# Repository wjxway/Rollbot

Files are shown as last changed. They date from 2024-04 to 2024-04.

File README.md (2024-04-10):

# Rollbot: a Spherical Robot Driven by a Single Actuator

Paper can be fetched from [Arxiv](https://arxiv.org/abs/2404.05120).

This repo is the full implementation of Rollbot, including complete hardware, software, theoretical derivation files.

It's still under construction, so the files might be a bit messy. I will clean it up once the paper is officially accepted.

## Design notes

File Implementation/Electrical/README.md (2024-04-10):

This is just a power converter from 4s battery down to 3.3V. Feel free to create your own.

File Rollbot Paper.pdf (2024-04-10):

## Rollbot: a Spherical Robot Driven by a Single Actuator

Jingxian Wang¹

and Michael Rubenstein¹

Abstract— Here we present Rollbot, the first spherical robot capable of controllably maneuvering on 2D plane with a single actuator. Rollbot rolls on the ground in circular pattern and controls its motion by changing the curvature of the trajectory through accelerating and decelerating its single motor and attached mass. We present the theoretical analysis, design, and control of Rollbot, and demonstrate its ability to move in a controllable circular pattern and follow waypoints.

I. INTRODUCTION

Underactuated robots has attracted researchers’ attention in recent years due to their advantages such as energy savings, material savings, space savings, etc. [1]. While underactuated systems like inverted pendulum [2, 3], underactuated hands [4, 5], and underactuated wrists [6, 7] have been extensively studied, few mobile robots have adopted the idea of underactuation due to the difficulty of designing movement mechanism that can utilize non-holonomic constraints and precisely controlling underactuated systems. Until now, only a handful of mobile robots can maneuver in 2D or 3D space with a single actuator. Robots in [8–10] used compliant mechanisms or one-way bearing to allow a single actuator to achieve multiple functions or have multiple mode of operation, effectively ‘multiplexing’ the actuator to move in space. Walking robot in [11] controls its movement by controlling left and right leg’s step size. Robots in [12– 15] and drones in [16, 17] move by rotating their body and accelerate forward at the appropriate time. Among all these works, only [15] proposed a wheeled robot, and it is also the only ground robot that do not move in discrete steps. Another key inspiration of our work is spherical robots
[18] studied for their structural simplicity and the inherent protective nature of their spherical shells that shields the internal mechanisms and electronics from hostile environments. Since the pioneering Rollo robot [19], three major types of rolling robot driven mechanisms has been proposed [18], including barycentric type [20, 21] that moves masses attached to pendulums or tracks around the robot, conservation of the angular momentum (CoAM) type [22] that uses reaction wheels or gyroscopes, and shell deformation type [23] that changes the shape of the shell. Interestingly, no existing spherical robot of any driving type have only one actuator to authors’ knowledge, and even the authors of review paper [18] claimed that ‘For a robot to be able to move in more than one direction, at least two DoFs are needed.’

1
Jingxian Wang and Michael Rubenstein are with the Center for Robotics and Biosystems, Northwestern University, Evanston, IL 60601, USA jingxianwang2026@u.northwestern.edu, rubenstein@northwestern.edu

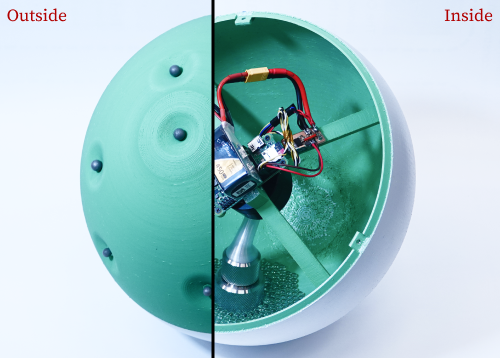
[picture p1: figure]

Fig. 1. Photo of inside and outside of Rollbot. Rollbot has a outer diameter of 24 cm and weighs 1.2 kg.

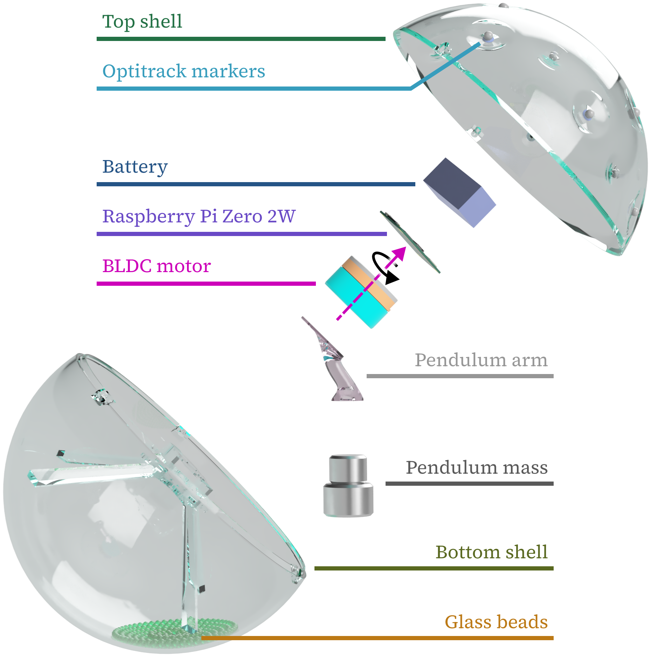
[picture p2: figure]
Bottom shell; Glass beads; Pendulum mass; Pendulum arm; Top shell; Optitrack markers; Battery; Raspberry Pi Zero 2W; BLDC motor

Fig. 2. An exploded view of Rollbot. The only actuator is the BLDC motor at the center which can rotate around the purple axis.

The lack of research in single actuator spherical robots motivates us to create Rollbot, a barycentric type spherical robot driven by a pendulum attached to a single motor. Rollbot can move on 2D plane by exploiting the non-holonomic rolling constraint.

II. ROBOT DESIGN

Rollbot, as shown in Fig. 1 and 2, sets out to test the feasibility of utilizing non-holonomic rolling constraint to achieve 2D motion using only a single motor actuator. RollBot is composed of a spherical shell and a pendulum connected to the shell through a motor. As the motor rotates the pendulum, The shell will also roll on the ground, and we can control the motion of Rollbot by changing the rotating speed of the motor. For concision, we will refer to the spherical shell as the shell, the pendulum mass as the mass, and the motor’s spinning speed as driving speed in future discussions.

A. Dynamics of Rollbot

Rollbot can be considered as a spherical rolling robot driven by a internal mass moving on a circular trajectory in the shell’s reference frame. In this section, we will derive the dynamics of a general spherical rolling robot driven by the movement of internal point masses and apply the result to Rollbot. We will start with a simple case where a spherical symmetric shell is driven by one internal point mass as illustrated in Fig. 3. We also assume that the robot will not lose contact with the ground and will not slip.

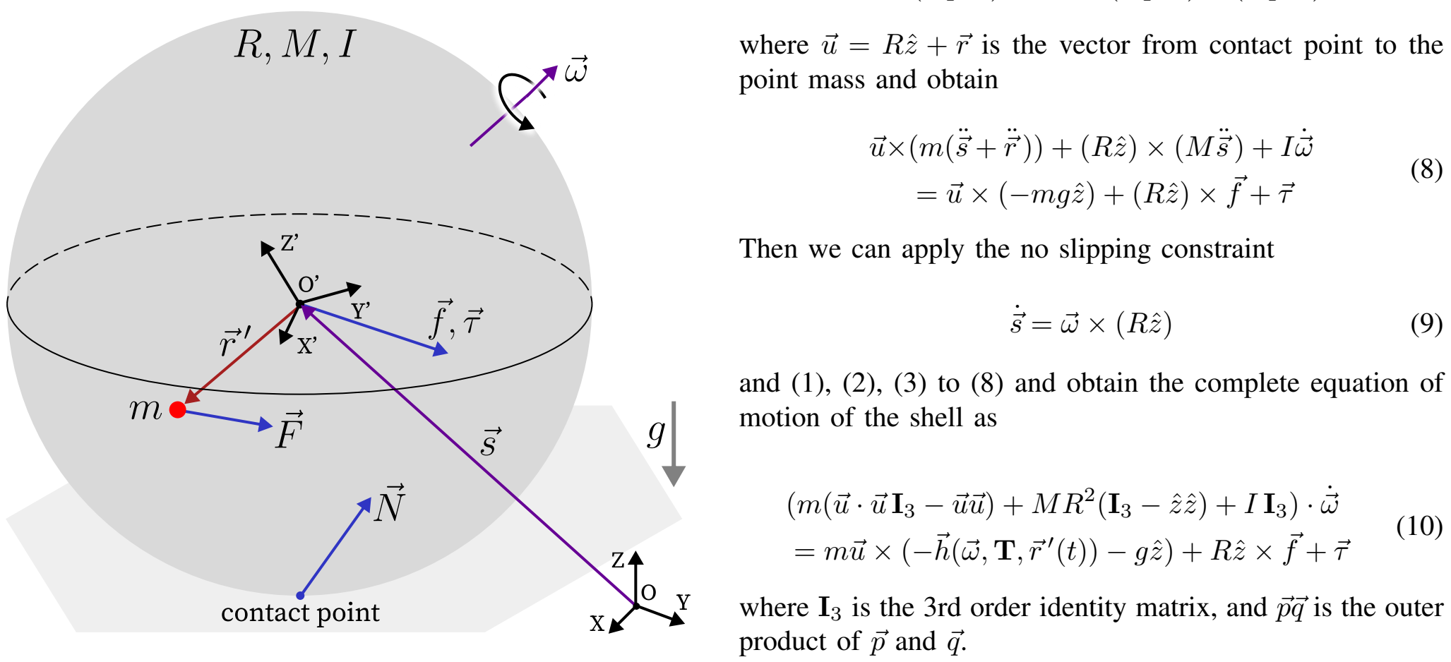
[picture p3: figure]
contact point; point mass and obtain; ˙⃗s = ⃗ω × (Rzˆ); motion of the shell as; (m(⃗u · ⃗u I3 − ⃗u⃗u) + MR²; (I3 − zˆzˆ) + I I3) ·; (t)) − gzˆ) + Rzˆ × ⃗f + ⃗τ; product of ⃗p and ⃗q.

Fig. 3. Illustration of relevant quantities. O-XYZ is the ground reference frame G, O’-X’Y’Z’ is the shell’s body reference frame B. ⃗s is the position of the center of the shell in G, ⃗ω is the angular velocity of the shell in G, and ⃗r ′
is the position of the mass in B. R, M, I are the radius, mass, and the moment of inertia of the shell respectively, and m is the mass of the point mass. f, ⃗τ ⃗ are the externally applied force and torque on the shell with respect to O′

, N⃗ is the sum of normal and friction force ground applies on the shell, and F⃗ is the force shell applies on the point mass.

The vector from the center of shell to the point mass O′m in ground frame, ⃗r, could be described using the rotation matrix T from body frame to ground frame as

⃗r = T · ⃗r ′
(1)

We can take its first and second derivative and obtain

˙⃗r =⃗ω × (T · ⃗r ′
) + T ·

˙⃗r ′
(2)
¨⃗r = ˙⃗ω × (T · ⃗r ′
)
+ (⃗ω × (⃗ω × (T · ⃗r ′
)) + 2⃗ω × (T ·

˙⃗r ′
) + T ·

¨⃗r ′
)
= ˙⃗ω × (T · ⃗r ′

) + ⃗h(⃗ω, T, ⃗r ′
(t)) | (3)

where a˙ is the derivative of a over time. Notice that term ⃗h is the inertial force applied on the point mass in the non-accelerating co-rotating frame and does not involve acceleration of the shell.
Newton’s second law and angular momentum theorem give us the equation of motion of the point mass and the shell.

m(

¨⃗s + ¨⃗r) = F⃗ − mgzˆ | (4)
M¨⃗s = −F⃗ + N⃗ − Mgzˆ + ⃗f | (5)

I

˙⃗ω = −(⃗r − ⃗s) × F⃗ + (−Rzˆ) × N⃗ + ⃗τ (6)

We could cancel out F⃗ and N⃗ by merging the three equations

⃗u × (Eqn.4) + Rzˆ × (Eqn.5) + (Eqn.6) | (7)

where ⃗u = Rzˆ + ⃗r is the vector from contact point to the

¨⃗s + ¨⃗r )) + (Rzˆ) × (M¨⃗s ) + I

˙⃗ω

= ⃗u × (−mgzˆ) + (Rzˆ) × ⃗f + ⃗τ

(8)

Then we can apply the no slipping constraint

and (1), (2), (3) to (8) and obtain the complete equation of

where I3 is the 3rd order identity matrix, and ⃗p⃗q is the outer

The physical meaning of (10) is clear: the left hand side is the moment of inertia matrix of the whole robot with respect to the contact point at this moment applied on the angular acceleration, and the right hand side is the torque applied on the robot with respect to the contact point contributed by the point mass’s inertia in the non-accelerating co-rotating frame, the point mass’s gravity, and the external force and torque applied on the shell.
We can also write out the supporting and friction force

N⃗ = (M + m)

¨⃗s + m¨⃗r + (M + m)gzˆ − ⃗f (11)

The condition for the robot to not jump and not slip could be expressed as

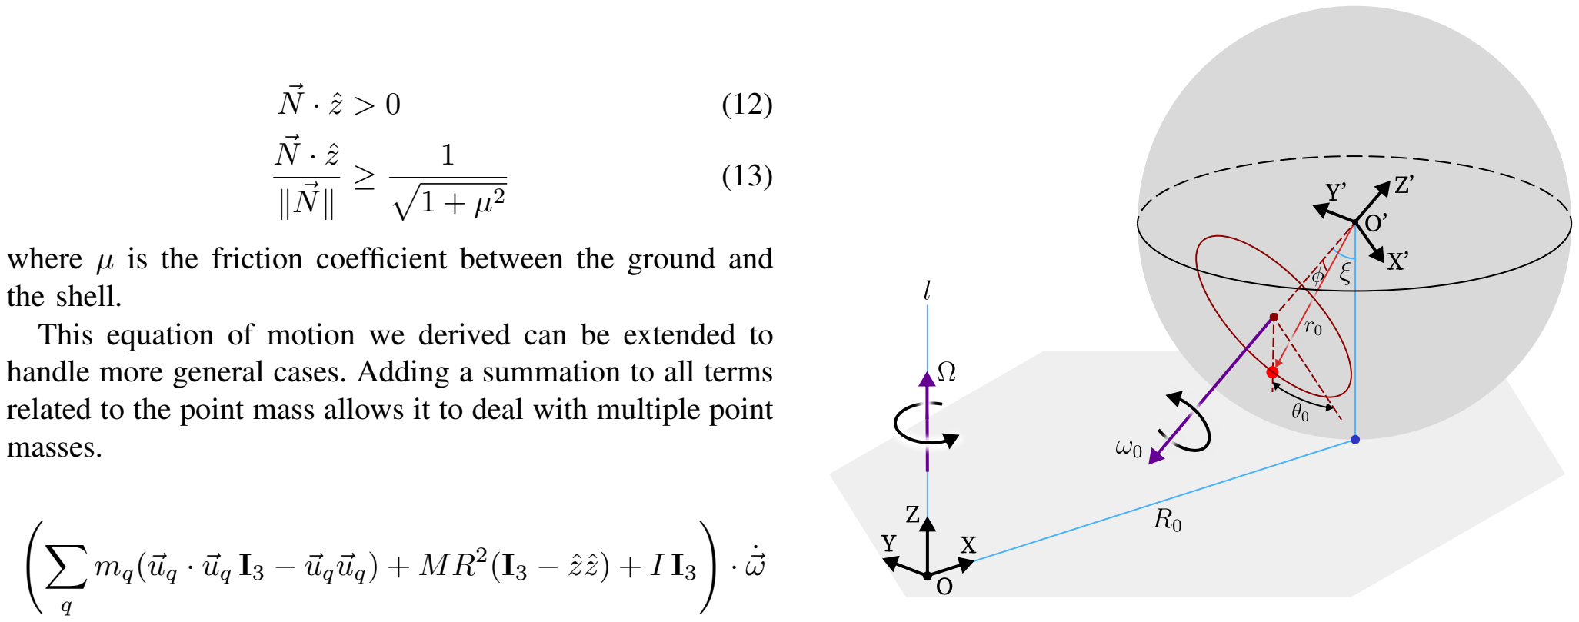
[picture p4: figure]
the shell.; masses.; mq(⃗uq · ⃗uq I3 − ⃗uq⃗uq) + MR²; (I3 − zˆzˆ) + I I3

where µ is the friction coefficient between the ground and

This equation of motion we derived can be extended to handle more general cases. Adding a summation to all terms related to the point mass allows it to deal with multiple point

=

X

q

mq⃗uq × (−⃗h(⃗ω, T, ⃗r ′
q

(t)) − gzˆ) + Rzˆ × ⃗f + ⃗τ

(14)
where mq is the mass of qth point mass, ⃗r ′
q

is the position
of qth point mass in B, and ⃗uq is the vector from the contact point to qth point mass. Furthermore, by distributing extra point masses fixed to the shell or other point masses, (14) can also deal with cases involving non-symmetrical mass distribution of shell or general solid bodies moving inside the robot.
The result we obtained is equivalent to what is proposed in [24], but the derivation is more straight forward and has clearer physical meaning.
When applying the model to Rollbot’s case, a good approximation would be directly use (10) and let

⃗r ′ = r0(sin ϕ cos θ(t) ˆx + sin ϕ sin θ(t) ˆy − cos ϕ zˆ) (15)

⃗τ = −k0⃗ω | (16)
⃗f = 0 | (17)
M = Ms + mb | (18)

where θ(t) is the rotating angle of the pendulum mass around Z

′
axis, and k0 is an an experimentally determined damping constant. Such simplification is valid when
- The shell has moment of inertia matrix in the form of I I3.
- The pendulum mass’s size is much smaller than |⃗r ′ |
and the radius of the shell R, so we can simplify the pendulum mass to a point mass.
- The damping on shell’s motion is small and have small impact on the behavior of Rollbot.
and we will show that our system satisfy these requirements in section II-D.
B. Quasi-Static State of Rollbot

In our experiments, we are slowly accelerating and decelerating the pendulum mass, so Rollbot is close to the quasi-static state where the driving speed θ

′
(t) = ω0 is a constant.
In the quasi-static state, Rollbot will revolve around a vertical

Fig. 4. Illustration of quasi-static state at t = 0. O-XYZ is the non-moving ground reference frame G with origin at the intersection of revolving axis l and ground plane, and X axis pointing towards the contact point. O’-X’Y’Z’ is the shell’s body reference frame B with Y’ axis parallel to Y

′
axis and Z’
aligned with the rotation axis of the motor and on X-Z plane, and the angle between Z and Z’ is ξ. The shell is revolving around l at angular velocity Ωˆz, plus the shell itself is also spinning at angular velocity ⃗ωs = −ω0zˆ

′
in quasi-static state. The shell’s revolving radius is R0.

axis l, and in the frame revolving together with the Rollbot, Rollbot’s movement is always the same, as shown in Fig. 4. Because the whole system is revolving around l at constant angular velocity Ω, we have

⃗u(t) = Tr(t) · ⃗u(0) | (19)
⃗ω(t) = Tr(t) · ⃗ω(0) | (20)

where Tr(t) is the rotation matrix defined as

Tr(t) =

cos(Ωt) − sin(Ωt) 0
sin(Ωt) | cos(Ωt) | 0
0 | 0 | 1
- (21)

Using this property, we can then express (10) using only variables at t = 0, and subsequently reduce it into three equations about Ω, θ0, and ξ.

m⃗u × (−g⃗z + Ω²
(R0xˆ + ⃗u − (⃗u · zˆ)ˆz) + MΩ

2R0Ryˆ

− k0(−ω0zˆ

′ + Ωˆz) + IΩω0 sin ξyˆ = 0

(22)

where R0 = ω0R sin ξ/Ω and zˆ

′ = sin ξxˆ + cos ξzˆ. The quasi-static state of Rollbot at different driving speed ω0 can then be obtained by numerically solving (22). The solution with Rollbot’s actual physical parameters is shown in Fig. 5. Fig. 5 shows that the revolving radius R0 starts from R tan ϕ when ω0 = 0, and gradually increases with ω0, hinting that we could control the trajectory of Rollbot by changing the driving speed. ξ starts from ϕ when ω0 = 0 and gradually approaches π/2, meaning that when Rollbot is almost moving straight forward when rolling fast. θ0 is close to 0, meaning that the pendulum mass is always near the bottom of the shell when driving speed is smaller than 3π.

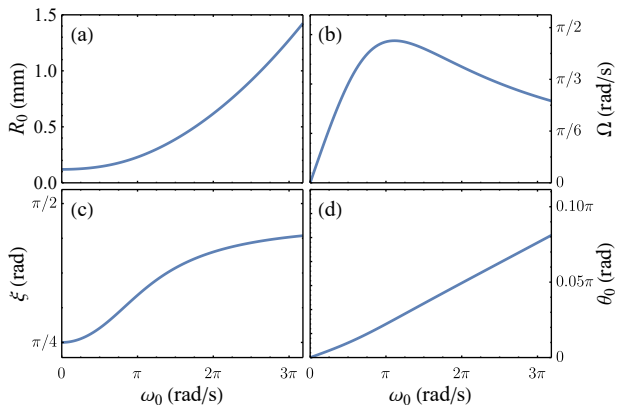
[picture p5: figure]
Ω (rad/s); ξ (rad); ω0 (rad/s); θ0 (rad)

Fig. 5. Plots of key parameters of quasi-static state versus driving speed ω0. (a) to (d) show the trends of revolving radius R0, revolving angular velocity Ω, tilting angle of rotating axis of the motor ξ and rotating angle of pendulum mass θ0 respectively.

Furthermore, we could also discover that as long as damping coefficient k0 is not exceedingly large, it has little impact on the result. This means that we can make assumption (16) for convenience of computation without influencing the result significantly.
Aside from the state shown above, there is also another set of ‘fast revolving state’, where θ0 is close to π and Rollbot revolves in the opposite direction at a much smaller radius. This set of state can rarely be observed in experiments.
C. Perturbation around Quasi-Static State

Perturbation around the quasi-static state tells us how stable the quasi-static state is and the response of Rollbot if we deviate from the state, either during acceleration and deceleration or due to external disturbances. In further derivation, we will use a

p
to represent a perturbed physical quantity a and δa to represent the perturbation of a, i.e. δa = a

p−a. We will only consider the first order perturbation in the following discussion.
We can apply a perturbation to the rotation matrix T and have

T

p
(t) = (1 + [Tr(t) · ⃗α(t)]) · T(t) | (23)

where ⃗α is a small perturbation vector, and [⃗α] is the skewsymmetric form of ⃗α. According to the definition, we have

δ⃗u = δ⃗r = (Tr · ⃗α) × ⃗r
= Tr · (⃗α × ⃗r(0)) | (24)
δ⃗ω = (Tr · ⃗α) × ⃗ω + dt(Tr · ⃗α)
= Tr · (⃗α × ⃗ωs(0) + ˙⃗α) | (25)

Put (24) and (25) into (9) and we have

δ

˙⃗s = Tr · ((⃗α × ⃗ωs(0) + ˙⃗α) × (Rzˆ)) | (26)

Take perturbation of (8), left multiply by T⁻¹
r

and use (26)
then we have

m(⃗α × ⃗r(0)) × (

¨⃗u(0) + ¨⃗s(0))

+ m⃗u(0) × Ω

2
(⃗α × ⃗r(0) − ((⃗α × ⃗r(0)) · zˆ)ˆz)

+ m⃗u(0) × (2Ωˆz × (

˙⃗α × ⃗r(0)) + ¨⃗α × ⃗r(0))

+ (m⃗u(0) + MRzˆ) × (( ˙⃗α × ⃗ωs(0) + ¨⃗α) × (Rzˆ))

+ I(

˙⃗α × ⃗ωs(0) + ¨⃗α)

+ mg(⃗α × ⃗r(0)) × zˆ
+ k0(⃗α × ⃗ωs(0) + ˙⃗α) = 0

(27)

Notice that this is an second order ordinary differential equation group of ⃗α(t) and the parameters are not dependent on time, we could plug in the values obtained in section II-B and obtain an equation in the following form

˙⃗α
¨⃗α
=
0 | I3
A3×3 | B3×3
·
⃗α
˙⃗α
(28)

The recovery behavior of Rollbot under perturbation is characterized by eigenvalues of the matrix in (28).
In addition, notice that the system will be identical if we make a perturbation and let Rollbot revolve around l by a certain angle, we should remove the eigenvalue and eigenvector corresponding to this mode of movement when analyzing the stability. Finally, we can conclude that if all but one eigenvalues have real part smaller than 0, then Rollbot is stable under perturbation and the characteristic time of recovery τ is determined by the eigenvalue λ2 with second smallest real part.

τ ≈ −

1
Re(λ2)

(29)

Plot of eigenvalues’ distribution under different ω0 with Rollbot’s actual physical parameters is shown in Fig. 6, showing that with our choise of parameters, Rollbot is able to recover from perturbations with characteristic time of about 7 s. This is consistent with the result in direct numerical simulation as well as our experiments.

-10

-5

0

5

10

Im

-1.0 | -0.8 | -0.6 | -0.4 | -0.2 | 0.0
Re

Fig. 6. Plot of eigenvalues’ trajectory for ω0 ∈ [0, 3π].

As far as the authors know, this is the first time quasi-static state and perturbation behavior are analyzed for spherical robots.

D. Hardware Design
When designing the hardware, we want it to satisfy the following criterion:
- Rollbot should be as close to our theoretical model as possible, i.e. satisfying the criteria given in section II-A.
- Rollbot should be close to quasi-static state even when accelerating/decelerating.
- Rollbot’s trajectory should change significantly as we accelerate/decelerate the motor.
The first criteria require us to design the Rollbot shell’s center of mass near the shell’s geometric center, a moment of inertia in the form of I0I3, and pendulum mass small enough to be considered as a point mass, and the second requires Rollbot to have fast recovery from transient state, and third requires revolving radius R0 to change significantly when we change the driving speed ω0.
We designed the diameter of Rollbot’s shell to be 24 cm, which is a few times larger than the scale of the battery and the motor, and concentrated the mass at the spherical surface of the shell. This make sure that the moment of inertia is dominated by the surface of the shell instead of its internal structures, keeping the moment of inertia in the form of I0I3. Furthermore, we also carefully positioned the motor and the battery to keep the center of mass near the the shell’s geometric center. The pendulum mass is made of stainless steel and is small comparing to the distance between it and the center of the shell as well as the size of the shell. We put mb = 40 g of glass beads in the shell so the collision between beads can introduce energy dissipation and create damping. Because the total mass of the beads is much smaller than the pendulum mass or the shell, and beads are always staying near the bottom of the shell, we can simplify the beads’ effect to an addition of mass to the shell plus a linear damping given by (16).
With the analysis in section II-C, we find out that the system is more stable when r0, m, ϕ, and k0 are larger. As such, we placed the pendulum mass as close to the shell as possible, and introduced the beads inside the shell. Experimentally, comparing to the case where no beads are added, Rollbot’s quasi-static dynamics is almost the same while exhibiting much less oscillation and much faster recovery after acceleration and deceleration.
With the analysis in section II-B, we could notice that the revolving radius R0 changes more significantly with ω0 when ϕ and m is smaller. This is the opposite with the analysis in the previous paragraph. Eventually, we chose a balanced parameter shown in Table. I, which allows Rollbot to vary its revolving radius from 0.12 m to 1.28 m when ω0 ∈ [0, 3π] and recover from transients within a few seconds.
E. Control Design
We already have a robot that can roll on the ground in circular pattern and theory derived in section II-B tells us
Quantity | Value | Explanation
R M I ϕ r m mb k0 | 0.12 m 0.840 kg 0.0053 kg · m² 45◦ 0.093 m 0.306 kg 0.040 kg (0.4 s⁻¹ )MR² | Outer radius of shell Mass of shell Moment of inertia of shell Angle between the pendulum mass, center of shell and the axis of motor Distance between pendulum mass’s center of mass and center of shell Mass of pendulum mass Total mass of beads Friction coefficient

TABLE I

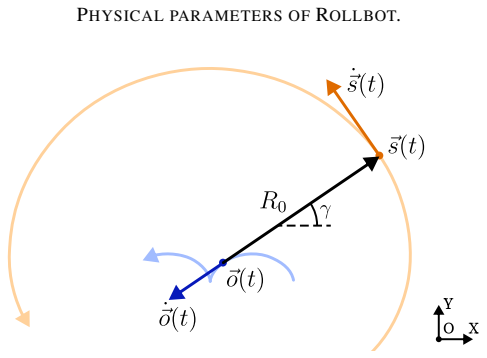
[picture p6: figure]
PHYSICAL PARAMETERS OF ROLLBOT.

Fig. 7. Illustration of relevant parameters in the control algorithm. The orange and blue curves are the trajectory of the center of the shell and the corresponding center of curvature respectively. At time t, the center of shell is at ⃗s (t), the center of curvature is at ⃗o (t) and the curvature radius is R0. The center of shell is moving at velocity ˙⃗s (t) along the curve perpendicular to ⃗s − ⃗o, and if Rollbot is accelerating, then the center of curvature will also move along ⃗s − ⃗o at a rate of ˙⃗o (t)

that the revolving radius R0 can be modulated by changing the driving speed ω0. In this section, we will derive a way of controlling Rollbot’s 2D motion by changing R0 at different times.
Instead of controlling the position ⃗s of Rollbot, we change to control the center of curvature ⃗o.
⃗o = ⃗s − R0{cos γ,sin γ, 0} | (30)

When Rollbot is rolling with a constant driving speed ω0, it will move in a circle, and the center of curvature will be stationary. However, if we accelerate the driving speed at a rate β at t = t0 when ⃗s − ⃗o is at angle γ, then the rate of change of curvature will be

˙⃗o | = vR0 =

dR0(ω)
dω
ω=ω0
β | (31)

and subsequently the velocity of center of curvature will be

˙⃗o = −vR0
{cos γ,sin γ, 0} | (32)

To move ⃗o towards a certain target position ⃗og, a simple solution could be

vR = −kp(⃗og − ⃗o) · {cos γ,sin γ, 0} | (33)

where kp > 0 is a constant coefficient. It is worth noting that in the experiments, ⃗o will not be the same as the actual center of curvature due to transient behavior of Rollbot. In reality, we need to consider the capability of the motor and various non-idealities. So, instead of using (33), we add a limit to the revolving radius to limit the driving speed, a limit to the maximum acceleration so we are always close to the quasi-static state, and use PID instead of simple proportional control to compensate for external interference like the slope of the ground and to keep the system stable. The control diagram is shown in Fig. 8.

(30) +

+

+

+

### PID

### PID

dot
product

acceleration
limit

Radius
limit

Fig. 8. Control diagram used in experiments. The input of the system are the current position ⃗s and orientation γ of the shell provided by the Optitrack system and the output is the target driving speed ω0.
So far we have been talking about how to control ⃗o instead of ⃗s. In case we want the robot to move across certain point ⃗sg at velocity ˙⃗sg, we only need to compute the corresponding target Rg using equations obtained in section II-B and target ⃗og using (30), and command Rollbot to roll around ⃗og at revolving radius Rg. If we want to stop the Rollbot at ⃗sg, we will first let it revolve around ⃗og and stop the motor when Rollbot is ∆t ≈ 0.15 s away from reaching ⃗sg, and the Rollbot will settle around ⃗sg.
| III. EXPERIMENTS

We conducted several experiments to demonstrate the ability of Rollbot. We used optitrack system to provide Rollbot with its real-time position and orientation, but all other computation are executed on-board.

A. Open-loop Motion
In the open-loop motion experiments, Rollbot will maintain a constant driving speed from 0 to 7 rad/s. We collect the revolving radius of the Rollbot under different driving speeds and compare it with the theoretical result obtained in section II-B to verify that our theory and approximation is consistent with reality. The results are shown in Fig. 9.
B. Stable Circular Motion
In the stable circular motion experiments, Rollbot will try to circle around a set point with a given radius ranging from 20 cm to 65 cm. Fig. 10 shows how Rollbot can start from a point far away from the setpoint and move towards the goal, and Fig. 11 shows the trajectory of Rollbot when it is stably revolving around the set point.
From Fig. 10 we can see that Rollbot move towards set point by having higher driving speed when moving towards

(a)

0.2

0.4

0.6

0.8

R0 (m)

ω0 (rad/s)

(c)

ξ (rad)

ω0 (rad/s)

(d)

Ω (rad/s)

ω0 (rad/s)

Fig. 9. Comparison between the theoretical and experimental results. Theoretical curves are drawn in blue lines and experimental results are drawn in
purple points. The slight systematic difference | between experimental data
and theoretical prediction of R0 and ξ (the | difference is 6 mm and 1

◦
respectively) are caused by the slight imbalance of the shell.

(a)

-0.8

-0.6

-0.4

-0.2

0.0

0.2

0.4

Y (m)

-0.8 | -0.6 | -0.4 | -0.2 | 0.0 | 0.2 | 0.4
X (m)

(b)

-0.5

0.0

0.5
X (m)

(c)

-0.5

0.0

0.5
Y (m)

(d)

2

4

## ω0 (rad/s)

0 | 20 | 40 | 60 | 80 | 100 120 140
t (s)

Fig. 10. Trajectory of Rollbot when moving towards the set point. (a) shows the trajectory, where the red circle shows the target radius Rg = 0.35 m, and the orange and blue lines are the trajectory of Rollbot and the ⃗o respectively. (b), (c), and (d) shows the change of variables over time, where the orange and blue lines represent the position of Rollbot and the ⃗o respectively and the green line represent the driving speed.

(a) | (b)
(c) | (d)

-0.5

0.0

0.5

Y (m)

-0.5

0.0

0.5

Y (m)

-0.5 | 0.0 | 0.5
X (m)
-0.5 | 0.0 | 0.5
X (m)

Fig. 11. Trajectory of Rollbot when stably revolving around the set point at {0,0}. Target revolving radius Rg is 0.20, 0.35, 0.50, 0.65 m for (a) to
(d) respectively.

the set point and vice versa. In this example, Rollbot moves at an average speed of approximately 2 cm/s when moving towards the set point. Once it reached the stably revolving state, it will still modulate the driving speed slightly to compensate for the slope of the ground.

C. Moving between Waypoints
We would also like to demonstrate the Rollbot’s ability to maneuver between waypoints, so we programmed Rollbot to move in a ‘N’ shape and stop at the four vertexes. The results in Fig. 12 shows that Rollbot could successfully move towards waypoints and stop within 7 cm of the targets.

IV. CONCLUSION
In this paper, we presented Rollbot, a single actuator spherical robot capable of controlled rolling motion on the ground. We provided a general mechanical analysis of spherical rolling robots driven by internal masses and the quasi-static state and stability analysis of Rollbot. Based on our theory, we designed Rollbot’s hardware and control algorithm and successfully achieved stable circular motion and waypoint following. Through experiments, we also verified our theory’s accuracy.
In future work, we plan to integrate an IMU on board to eliminate the need of using external Optitrack system, and we also plan to investigate more on how to design the control and path planning algorithm to make it move faster towards targets, have less steady state error, and potentially maneuver around obstacles or non-flat surfaces. With these future additions, Rollbot would be the simplest yet still powerful spherical robot, making it a great testbed for underactuated robotics and related fields.

Start

End

-1.0

-0.5

0.0

0.5

1.0

Y (m)

-1.0 | -0.5 | 0.0 | 0.5 | 1.0
X (m)

Fig. 12. Experimental results for waypoint movement experiment. Purple line shows the target trajectory of ⃗o, red and orange crosses are the target and actual stopping points.

REFERENCES
[1] Bin He, Shuai Wang, and Yongjia Liu. “Underactuated Robotics: a Review”. In: International Journal of Advanced Robotic Systems 16.4 (2019),
p. 1729881419862164.
[2] Olfa Boubaker. “The Inverted Pendulum Benchmark in Nonlinear Control Theory: a Survey”. In: International Journal of Advanced Robotic Systems 10.5 (2013), p. 233.
[3] Yanbin Feng Hongxing Li Jiayin Wang and Yundong Gu. “Hardware Implementation of the Quadruple Inverted Pendulum with Single Motor”. In: Progress in Natural Science 14.9 (2004), pp. 822–827.
[4] Clement Gosselin, Frederic Pelletier, and Thierry Laliberte. “An Anthropomorphic Underactuated Robotic Hand with 15 DOFs and a Single Actuator”. In: ICRA. 2008, pp. 749–754.
[5] Tadaaki Hasegawa et al. “Powerful and Dexterous Multi-finger Hand Using Dynamical Pulley Mechanism”. In: ICRA. 2022, pp. 707–713.
[6] Wu Licheng, Kong Yanxuan, and Li Xiali. “A Fully Rotational Joint Underactuated Finger Mechanism and Its Kinematics Analysis”. In: International Journal of Advanced Robotic Systems 13.5 (2016).
[7] Raffaele Di Gregorio. “Kinematic Analysis of the (nS)-2SPU Underactuated Parallel Wrist”. In: Journal of Mechanisms and Robotics 4.3 (June 2012),
p. 031006.
[8] David Zarrouk and Ronald S Fearing. “Compliancebased Dynamic Steering for Hexapods”. In: IROS. IEEE. 2012, pp. 3093–3098.
[9] Evandro Bernardes, Frédéric Boyer, and Stéphane Viollet. “Modelling, Control and Simulation of a Single Rotor UAV with Swashplateless Torque Modulation”. In: Aerospace Science and Technology (2023),
p. 108433.
[10] Jianguo Zhao et al. “MSU Jumper: A Single-motoractuated Miniature Steerable Jumping Robot”. In: IEEE Transactions on Robotics 29.3 (2013), pp. 602– 614.
[11] James Kyle et al. “The Simplest Walking Robot: A Bipedal Robot with One Actuator and Two Rigid Bodies”. In: 2023 IEEE-RAS 22nd International Conference on Humanoid Robots (Humanoids). IEEE. 2023, pp. 1–7.
[12] Gedaliah Knizhnik and Mark Yim. “Thrust Direction Control of an Underactuated Oscillating Swimming Robot”. In: IROS. 2021, pp. 8665–8670.
[13] Andrew SaLoutos and Michael Rubenstein. “Spin-Bot: An Autonomous, Externally Actuated Robot for Swarm Applications”. In: Distributed Autonomous Robotic Systems. Springer, 2019, pp. 211–224.
[14] Jingxian Wang and Michael Rubenstein. “PCBot: a Minimalist Robot Designed for Swarm Applications”. In: IROS. IEEE. 2022, pp. 1463–1470.
[15] Satoshi Ito et al. “An Autonomous Mobile Robot with Passive Wheels Propelled by a Single Motor”. In: Robotics and Autonomous Systems 122 (2019),
p. 103310.
[16] Weixuan Zhang, Mark W Mueller, and Raffaello D’Andrea. “A Controllable Flying Vehicle with a Single Moving Part”. In: ICRA. 2016, pp. 3275–3281.
[17] Andrew G Curtis et al. “Autonomous 3D Position Control for a Safe Single Motor Micro Aerial Vehicle”. In: IEEE Robotics and Automation Letters (2023).
[18] Aminata Diouf et al. “Spherical Rolling Robots -Design, Modeling, and Control: a Systematic Literature Review”. In: Robotics and Autonomous Systems (2024), p. 104657.
[19] Aarne Halme, Torsten Schonberg, and Yan Wang. “Motion Control of a Spherical Mobile Robot”. In: Proceedings of 4th IEEE International Workshop on Advanced Motion Control. Vol. 1. IEEE. 1996, pp. 259–264.
[20] Puyan Mojabi et al. “Introducing August: a Novel Strategy for an Omnidirectional Spherical Rolling Robot”. In: ICRA. Vol. 4. IEEE. 2002, pp. 3527–3533.
[21] Jiazhen Chen et al. “Design and Motion Control of a Spherical Robot with Control Moment Gyroscope”. In: 3rd International Conference on Systems and Informatics (ICSAI). IEEE. 2016, pp. 114–120.
[22] Shourov Bhattacharya and Sunil K Agrawal. “Spherical Rolling Robot: A Design and Motion Planning Studies”. In: IEEE Transactions on Robotics and Automation 16.6 (2000), pp. 835–839.
[23] Keith W Wait, Philip J Jackson, and Lanny S Smoot. “Self Locomotion of a Spherical Rolling Robot Using a Novel Deformable Pneumatic Method”. In: ICRA. IEEE. 2010, pp. 3757–3762.
[24] Vakhtang Putkaradze and Stuart Rogers. “On the Dynamics of a Rolling Ball Actuated by Internal Point Masses”. In: Meccanica 53 (2018), pp. 3839–3868.

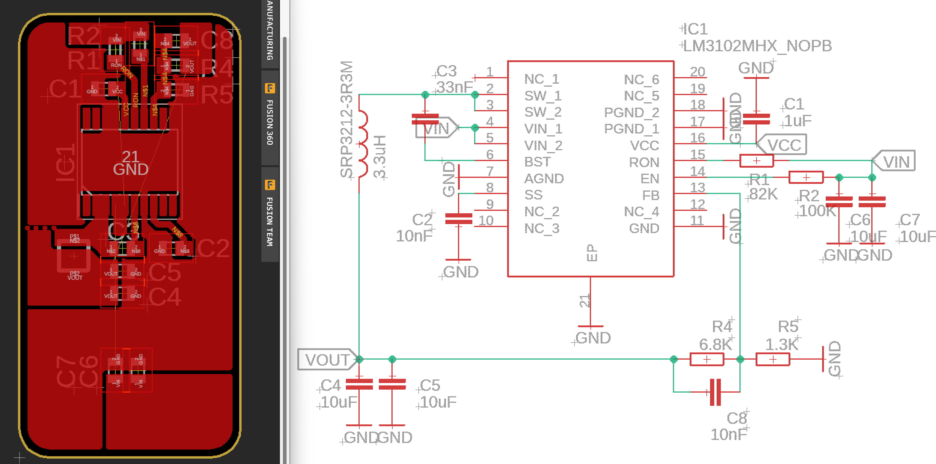
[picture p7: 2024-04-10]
Implementation/Electrical/Screenshot.png

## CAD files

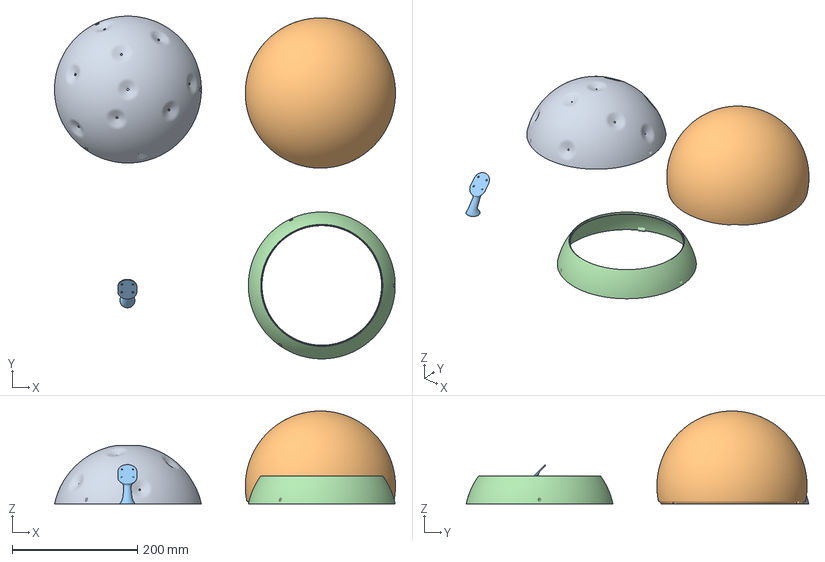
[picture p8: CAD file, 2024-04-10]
Implementation/Mechanical/3D Printing Files.3mf
544.8 x 547.6 x 148.6 mm
top shell_int.stl
bottom shell_int.stl
pendulum.stl
top shell_int

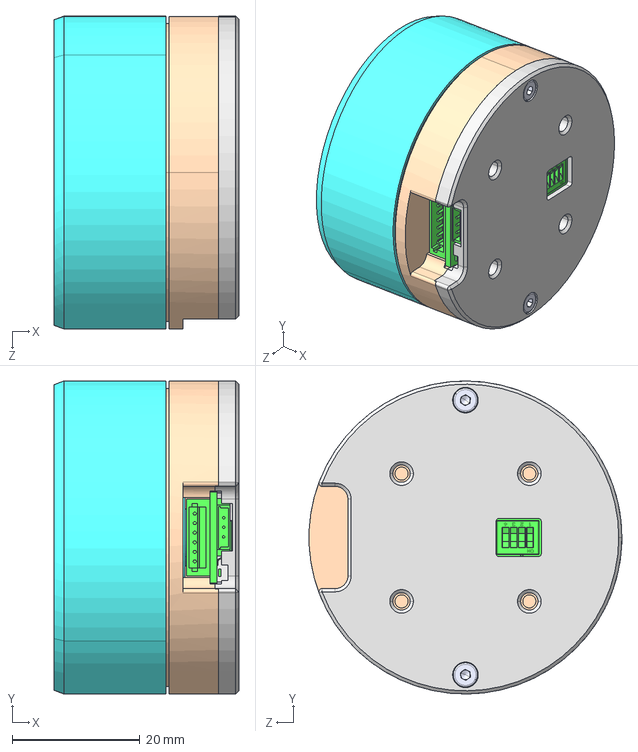
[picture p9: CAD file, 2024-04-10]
Implementation/Motor Specs/MS5010v2.STEP
28.9 x 49.0 x 49.0 mm

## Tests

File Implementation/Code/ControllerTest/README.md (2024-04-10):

# Rollbot Demo

## General Description

Rollbot is a single actuator robot that can move on the ground. It is driven by a single motor inside the robot that spins a pendulum mass, and you can control its motion by accelerating and decelerating the motor. For more details please check the paper:

[Rollbot: a Spherical Robot Driven by a Single Actuator (arxiv.org)](https://arxiv.org/abs/2404.05120)

In this demo you will be controlling motor's driving speed in an attempt to move the robot here and there (slamming into purge towers…) using a Xbox one controller. 

## System Description

To run this demo, you will need:

- A Rollbot of course!
- **ControllerTest** code running on the raspberry pi zero 2w controller.
- Rollbot connected to a Xbox one controller, preferably using Bluetooth.

For how to set up Bluetooth connection to Xbox one controller and how to compile and run the code, please refer to the additional information section.

## What To Bring Checklist

- [ ] Rollbot
- [ ] Stuff for Rollbot to run into (purge tower or something)
- [ ] Hex screw driver for opening up Rollbot
- [ ] Li-Po battery x2
- [ ] Li-Po battery charger
- [ ] Tape to attach the Li-Po batteries to Rollbot
- [ ] Xbox one Bluetooth Joystick
- [ ] Backup AA battery x2 for joystick

And if you really want to make sure it's not going to go wrong or if you want to adjust things on the go:

- [ ] Keyboard and adaptor
- [ ] Monitor, connector and adaptor (HDMI)
- [ ] Computer
- [ ] Phone for local network

## Commands

Once the Rollbot and controller are up and running, you should be able to control the Rollbot using buttons and triggers. There are three states for Rollbot:

1. **Disengaged**, where motor power is off and unless you really want to engage it, it won't accidentally engage. It should always be in this state on your hands !!!
2. **Engaged**, where the motor power is on but the motor is not spinning. Keep in this state before you hand the controller to the kids.
3. **Running**, where the motor power is on and the motor is spinning. 

Here is how you switch between the states and control the Rollbot:

1. **Disengaged -> engaged**. Press X and B at the same time while not pressing A and Y, hold for 1s.
2. **Engaged-> running**. Press left and right menu buttons (the two buttons between the left joystick and the ABXY pad, right below the xbox symbol) at the same time.
3. **Running or Engaged -> Disengaged**. Press LB and RB buttons (the two buttons above the left joystick and the ABXY pad) at the same time.
4. **Control**. By default, the control input is the RT button (the right analog trigger above the right joystick and RB). the harder you push the button, the faster the motor will rotate. Note that this is the analog signal, so you can have intermediate speeds if you wish to.
5. **Change control input**. By default, the control input is the RT button, but you can change it to other buttons or joysticks by pressing down A and left control pad's right upper, right lower, left upper or left lower controls at the same time. These four directions corresponds to the RT, right joystick's Y axis, LT, left joystick's Y axis respectively. For triggers, the harder you push down the faster the motor driving speed is; for joysticks, the higher Y axis is, the faster.
6.  **Quit program**. Hold A and Y but not B and X for 10s to quit the program. **Note that you should always quit this way or else you risk running multiple instances of pigpio library which might cause issues.**

## Additional Information

1. To build the ControllerTest and run the program, you will need cmake and make on the raspberry pi

   ```shell
   sudo apt update && sudo apt upgrade
   sudo apt install make
   sudo apt install cmake
   ```

   To build the code, run 

   ```shell
   cd xxx/ControllerTest
   cmake ./
   make ./ControllerTest
   ```

   And to run the code, run

   ```shell
   sudo ./ControllerTest
   ```

   If you want to make it auto start at the boot so you don't need a computer, in the source code `main.cpp` change the code to

   ```c++
   #define WAIT_FOR_CONNECTION 1
   ```

   and add the code to start on boot menu by

   1. Open the terminal and type the following command to open the rc.local file

      ```shell
      sudo nano /etc/rc.local
      ```

   2. In the `rc.local` file, enter the following line of code before the "exit 0" line, where xxx is the path to the ControllerTest folder (you can find that out using `ls -lrt -d -1 "$PWD"/{*,.*}`)

      ```
      sudo systemctl start bluetooth &
      sudo xxxxx/ControllerTest/ControllerTest &
      ```

   3. Hit **CTRL + S** to save the file.

2. To enable Bluetooth-based Xbox one joystick support on a fresh raspberry pi

   ```shell
   sudo apt install bluetooth pi-bluetooth bluez blueman
   bluetoothctl	
   ```

   Then put the Xbox one in pairing mode by long clicking the pairing button, and in bluetoothctl

   ```shell
   agent on
   scan on
   ```

   Then after you find the controller you want to connect to, remember its MAC address.

   ```shell
   pair [XX:XX:XX:XX:XX:XX]
   trust [XX:XX:XX:XX:XX:XX]
   ```

   Then you should be able to auto connect to this controller every time.

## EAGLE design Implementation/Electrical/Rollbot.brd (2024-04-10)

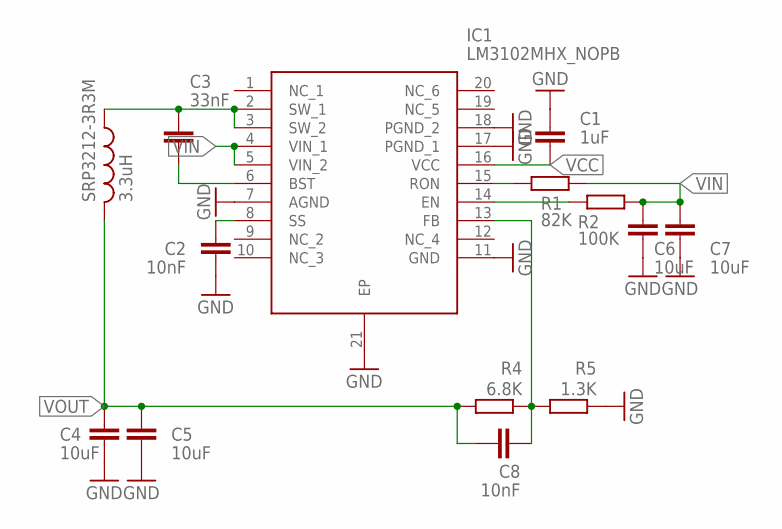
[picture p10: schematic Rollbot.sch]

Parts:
C1: 1uF; C0603
C2, C8: 10nF; C0603
C3: 33nF; C0603
C4, C5, C6, C7: 10uF; C0603
IC1: LM3102MHX_NOPB; SOP65P640X110-21N
R1: 82K; R0603
R2: 100K; R0603
R4: 6.8K; R0603
R5: 1.3K; R0603
SRP3212-3R3M: 3.3uH; SRP3212

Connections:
GND: C1.1, C2.1, C4.2, C5.2, C6.2, C7.2, IC1.7 (AGND), IC1.11 (GND), IC1.17 (PGND_1), IC1.18 (PGND_2), IC1.21 (EP), R5.1
unnamed: IC1.14 (EN), R2.1
unnamed: C3.1, IC1.2 (SW_1), IC1.3 (SW_2), SRP3212-3R3M.P$1 (1)
unnamed: C8.2, IC1.13 (FB), R4.1, R5.2
unnamed: C3.2, IC1.6 (BST)
unnamed: C2.2, IC1.8 (SS)
RON: IC1.15 (RON), R1.1
VCC: C1.2, IC1.16 (VCC)
VIN: C6.1, C7.1, IC1.4 (VIN_1), IC1.5 (VIN_2), R1.2, R2.2
VOUT: C4.1, C5.1, C8.1, R4.2, SRP3212-3R3M.P$2 (2)

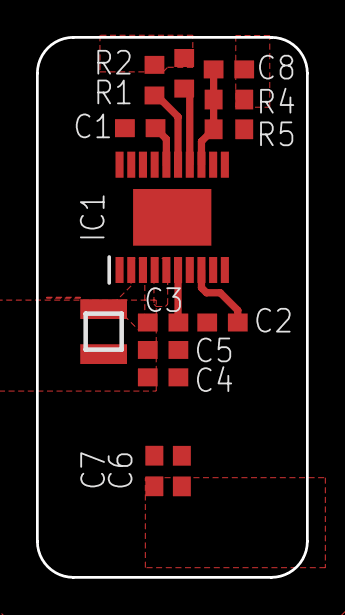
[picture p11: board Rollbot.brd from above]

Board: 2 copper layers, 15.0 x 30.0 mm, 14 parts (0 on the bottom side), 10 nets.

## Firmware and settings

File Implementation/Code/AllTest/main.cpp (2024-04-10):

#include "PrunedNatNet.hpp"
#include "motor.hpp"
#include <cstring>
#include <pigpio.h>

#include <iostream>
#include <fstream>
#include <iomanip>

#define _USE_MATH_DEFINES
#include <cmath>

using std::max;
using std::min;

// clip
float clip(float v, float min, float max)
{
    if(v<=min)
    {
        return min;
    }
    else if(v>=max)
    {
        return max;
    }

    return v;
}
float clip(float v, float maxabs)
{
    if(v<=-maxabs)
    {
        return -maxabs;
    }
    else if(v>=maxabs)
    {
        return maxabs;
    }
    
    return v;
}

// convert angle to [-pi,pi)
float angle_convert(float v)
{
    return v - (roundf(v/M_PI)*M_PI);
}

// convert value to [-18000,18000)
uint16_t frac_part(int32_t val)
{
    return uint16_t(val - int32_t(floor(float(val) / 36000.0F)) * 36000);
}

// angular velocity in rad/s
// radius in m
float rot_radius(const float angv)
{
    return 0.105374F + 0.013149F * angv * angv;
}

// angular velocity in rad/s
// revolving angular velocity in rad/s
float rot_Omega(const float angv)
{
    return angv / (0.123342F * angv * angv - 0.166428F * angv + 1.51782F);
}

// angular velocity in rad/s
// radius in m
float motor_angv(const float rot_radius)
{
    return sqrt((rot_radius - 0.105374F) / 0.013149F);
}

int main(int argc, char *argv[])
{
    // read ip address from input
    char szMyIPAddress[128] = "";
    char szServerIPAddress[128] = "";
    if (argc > 2)
    {
        strcpy(szServerIPAddress, argv[1]); // server IP
        strcpy(szMyIPAddress, argv[2]);     // local IP
    }
    else
    {
        printf("Usage:\n\n\tPacketClient [ServerIP] [LocalIP]\n");
        return 1;
    }

    // init optitrack interface
    int cond = Optitrack::Init(szMyIPAddress, szServerIPAddress);
    if (cond != 0)
    {
        printf("Optitrack init failure! code : %d\n", cond);
        return 1;
    }

    // init GPIO and lauch motor control
    Motor::Serial_open();
    Motor::Resume();
    Motor::Clear_loops();
    Motor::Set_multi_loop_position_2(0, 36000);
    gpioDelay(2000000);

    // setup log file
    std::fstream outputFile;
    // Open a file for writing
    outputFile.open("./log.csv", std::ios::out);
    if (!outputFile.is_open())
    {
        printf("Error opening the file!\n");
        return 1;
    }

    printf("Setup Complete!\n");

    // minimum delay time between mid exposure time and machine time
    int64_t time_delay = INT64_MAX;
    // first spend 5s to determine the delay between timestamp and local time
    for (int i = 0; i < 10000; i++)
    {
        // delay for 100us
        gpioDelay(100);

        // get data and print
        auto state = Optitrack::Get_state();
        int64_t delay = Get_time() - int64_t(state.cameraMidExposureTimestamp / 10);

        time_delay = std::min(time_delay, delay);
    }

    printf("Time delay min is %ld\nMain program Start!\n", time_delay);

    // main program
    // time step in s
    float time_step = 0.01F;
    // target point and radius in m
    float target_x = 0.00F, target_y = 1.6F, target_radius = 0.25F;
    // proportional coefficients in unit of (revolving radius in meters/ revolving angle in radians) / (position or radius error in meters)
    float kp_radius = 0.1F, kp_position = 0.15F;
    // integral coefficients in unit of (revolving radius in meters/ revolving angle in radians) / (position or radius error in meters * revolving angle in radians)
    float ki_radius = 0.003F, ki_position = 0.005F;
    // differential coefficients in unit of (revolving radius in meters/ revolving angle in radians) / (position or radius error in meters / revolving angle in radians)
    float kd_radius = 2.0F, kd_position = 2.0F;
    // derivative term filter constant, value should be 1 divide by angle constant
    float vel_update_const = 1.0F / (2.0F*M_PI);
    // prevent over compensation for radius integral term
    // float invert_amp = 1.0F;
    // maximum value of integral term in unit of meters*radians
    float i_radius_max = 60.0F, i_position_max = 60.0F;
    // maximum vel and acc
    // max acceleration is in unit of revolving radius in meters/revolving angle in radians
    // set max_acc to 0.25 or higher when target_radius is larger than 0.5m.
    float min_radius = 0.2F, max_radius = 1.5F, transition_radius = 0.5F, max_acc = 0.15F;

    outputFile << "delay, target_x, target_y, target_radius, kp_radius, kp_position, ki_radius, ki_position, kd_radius, kd_position, vel_update_const, i_radius_max, i_position_max, min_radius, max_radius, transition_radius, max_acc, time_step\n"
               << time_delay << " , " << target_x << " , " << target_y << " , " << target_radius << " , " << kp_radius << " , " << kp_position << " , " << ki_radius << " , " << ki_position << " , " << kd_radius << kd_position  << " , " << vel_update_const << " , " << i_radius_max << " , " << i_position_max << " , " << min_radius << " , " << max_radius << " , " << transition_radius << " , " << max_acc << " , " << time_step << "\nconventional pos {x,y} = exposure pos {x,-z}\n"
               << "local time, exposure time, set motor angv, exposure pos x, y, z, qx, qy, qz, qw, x_extrapolated, y_extrapolated, angle_extrapolated, xc, yc, ix, iy, ir\n";

    // starting time
    int64_t start_time = Get_time();

    // // code for stop test
    // // stop time in us, -1 means never stop
    // int64_t stop_delay = -1;// 150000000LL;
    // bool stopped = false;

    // code for waypoint following
    // {xc,yc}'s waypoints
    float waypoint[4][2]={{-0.90,0.75},{-0.90,2.00},{0.50,0.75},{0.50,2.00}};
    // stop at what angle at each waypoint
    float stop_angle[4]={-M_PI/2,M_PI/2,-M_PI/2,M_PI/2};
    // move, hold, and stop time in us
    int64_t move_time=120000000;
    int64_t hold_time=50000000;
    int64_t stop_time=25000000;
    // clear static variables
    bool clearvar = false;

    while (true)
    {
        // delay for 10ms
        gpioDelay(time_step*1000000.0F);

        // get data and print
        auto state = Optitrack::Get_state();
        auto curr_time = Get_time();

        // routine for waypoint changing
        static int waypoint_state = -1; // 10th digit, 0 for at waypoint 0, 1 for moving towards 1, etc.
                        // 1th digit, stage 0,1,2 -> currently is move, hold, stop. -1 is initial
        static int64_t state_start_time = curr_time;

        // whether we are in stopping state and have stopped already
        static bool stopped=true;

        // just a random buffer to pass out current angle
        static float angle_buf=0.0F;

        int stage=0; // temp var
        float tempratio;
        if(curr_time-(curr_time/1000000)*1000000<=15000)
        printf("time %.1f, state: %d -- %.1f\n",float(curr_time)/1000000.0F, waypoint_state,float(curr_time-state_start_time)/1000000.0F);
        switch(waypoint_state)
        {
        case -1:
            if(curr_time-state_start_time <= stop_time)
            {
                target_x=waypoint[0][0];
                target_y=waypoint[0][1];
            }
            else
            {
                // go to move to waypoint 1 routine
                state_start_time = curr_time;
                stopped=false;
                waypoint_state=10;
            }
            break;
        case 10:
        case 20:
        case 30:
            stage = waypoint_state/10;
            if(curr_time-state_start_time <= move_time)
            {
                tempratio=float(curr_time-state_start_time)/float(move_time);
                target_x=(1.0F-tempratio)*waypoint[stage-1][0]+tempratio*waypoint[stage][0];
                target_y=(1.0F-tempratio)*waypoint[stage-1][1]+tempratio*waypoint[stage][1];
            }
            else
            {
                // go to position holding routine
                state_start_time = curr_time;
                waypoint_state++;
            }
            break;
        case 11:
        case 21:
        case 31:
            stage = waypoint_state/10;
            if(curr_time-state_start_time <= hold_time)
            {
                target_x=waypoint[stage][0];
                target_y=waypoint[stage][1];
            }
            else
            {
                // go to stop routine
                state_start_time = curr_time;
                waypoint_state++;
            }
            break;
        case 12:
        case 22:
        case 32:
            stage = waypoint_state/10;
            if(curr_time-state_start_time <= stop_time)
            {
                if(!stopped)
                {
                    if(stop_angle[stage]-0.35<=angle_buf&&angle_buf<=stop_angle[stage]-0.15)
                    {
                        Motor::Set_velocity(0);
                        stopped=true;
                    }
                }
            }
            else
            {
                // go to stop routine
                state_start_time = curr_time;
                stopped=false;
                clearvar=true;
                waypoint_state+=8;
            }
            break;
        case 40:
            Motor::Set_velocity(0);
            printf("Program Stopped!");
            return 0;
        }


        if (state.bTrackingValid && !stopped)
        {
            // motor velocity in rad/s
            static float current_motor_vel = 0;
            static float last_radius = 0.15;
            if(clearvar)
            {
                current_motor_vel = 0;
                last_radius=0.15;
            }

            float angv = current_motor_vel;
            float current_radius = rot_radius(angv);
            float current_Omega = rot_Omega(angv);

            // {qx,qy,qz,qw} -> rotation matrix
            // rotation matrix.{0,0,1} -> {x0,y0,z0} is the spacial coordinates for the heading
            // arctan(x0,y0) -> its current heading
            float angle = atan2f(-0.5F+state.qx*state.qx+state.qy*state.qy, state.qx*state.qz + state.qy*state.qw);
            float angle_extrapolated = angle + current_Omega * (float(curr_time - time_delay - int64_t(state.cameraMidExposureTimestamp / 10)) * 0.000001F);

            angle_buf=angle_extrapolated;

            static float last_angle_extrapolated = angle_extrapolated;
            static int64_t last_time = curr_time;
            if(clearvar)
            {
                last_angle_extrapolated = angle_extrapolated;
                last_time = curr_time;
            }

            float x_extrapolated = state.x - current_radius*current_Omega* sin((angle + angle_extrapolated) / 2) * (float(curr_time - time_delay - int64_t(state.cameraMidExposureTimestamp / 10)) * 0.000001F);
            float y_extrapolated = -state.z + current_radius*current_Omega* cos((angle + angle_extrapolated) / 2) * (float(curr_time - time_delay - int64_t(state.cameraMidExposureTimestamp / 10)) * 0.000001F);

            // position of curvature center
            // notice that the X+ is Z- in optitrack streamed data
            //                 Y+ is X-
            float xc = x_extrapolated - current_radius * cos(angle_extrapolated);
            float yc = y_extrapolated - current_radius * sin(angle_extrapolated);

            float dtheta = max(float(fabs(angle_convert(angle_extrapolated - last_angle_extrapolated))),0.0001F);

            static float last_xc = xc, last_yc = yc;
            static float filt_vx = 0.0F, filt_vy = 0.0F, filt_vr = 0.0F;
            if(clearvar)
            {
                last_xc=xc;
                last_yc=yc;
                filt_vx=0.0F;
                filt_vy=0.0F;
                filt_vr=0.0F;
            }

            float vx = (xc - last_xc) / dtheta, vy = (yc - last_yc) / dtheta, vr = (current_radius-last_radius)/dtheta;
            float vel_update_factor = clip(vel_update_const * dtheta, 0.0F, 1.0F);
            filt_vx = (1.0F - vel_update_factor) * filt_vx + vel_update_factor * vx;
            filt_vy = (1.0F - vel_update_factor) * filt_vy + vel_update_factor * vy;
            filt_vr = (1.0F - vel_update_factor) * filt_vr + vel_update_factor * vr;

            // add position integral term when it's near target
            static float ix = 0.0F, iy = 0.0F, ir = 0.0F;
            if(clearvar)
            {
                ix=0.0F;
                iy=0.0F;
                ir=0.0F;

                clearvar=false;
            }

            ix += dtheta * (xc - target_x);
            iy += dtheta * (yc - target_y);
            ir += dtheta * (current_radius - target_radius);

            // limit integral term
            ix = clip(ix, i_position_max);
            iy = clip(iy, i_position_max);
            ir = clip(ir, i_radius_max);

            // compute the acceleration to command
            float pos_ar = (kp_position * (xc - target_x) + ki_position * ix + kd_position * filt_vx) * cos(angle_extrapolated) + (kp_position * (yc - target_y) + ki_position * iy + kd_position * filt_vy) * sin(angle_extrapolated);
            float rad_ar = - kp_radius * (current_radius - target_radius) - ki_radius * ir - kd_radius * filt_vr;
            float total_ar = pos_ar + rad_ar;

            // limit the radius's change!
            // float vlim = max_acc * max(tanh((current_radius-min_radius) / transition_radius), .1) * max(tanh((max_radius - current_radius) / transition_radius),.1);
            float vlim = max_acc;

            // print feedback info
            // printf("{%.3f,%.3f}.{%.3f,%.3f} -> %.3f + %.3f = %.3f < %.3f\n", (kp_position * (xc - target_x) + ki_position * ix + kd_position * filt_vx),(kp_position * (yc - target_y) + ki_position * iy + kd_position * filt_vy),cos(angle_extrapolated), sin(angle_extrapolated), pos_ar, rad_ar, total_ar, vlim);

            total_ar = clip(total_ar, vlim);

            // change the radius
            float new_radius = min(max_radius, max(min_radius, current_radius + total_ar * current_Omega * (curr_time - last_time)*0.000001F));

            // set new speed
            current_motor_vel = motor_angv(new_radius);
            if(current_motor_vel>=9.0F)
            {
                current_motor_vel=9.0F;
            }

            Motor::Set_velocity(int32_t(-current_motor_vel / M_PI * 18000.0F));

            // // for motor stop tests
            // if(stop_delay < 0 || curr_time - start_time <= stop_delay)
            // {
            //     Motor::Set_velocity(int32_t(-current_motor_vel / M_PI * 18000.0F));
            // }
            // else
            // {
            //     if(!stopped)
            //     {
            //         stopped = true;
            //         printf("Motor stopped!\n");
            //         outputFile << "\n\nMotor stopped!\n\n";
            //     }

            //     Motor::Set_velocity(0);
            // }

            // update those with last prefix
            last_angle_extrapolated = angle_extrapolated;
            last_time=curr_time;
            last_xc=xc;
            last_yc=yc;
            last_radius=current_radius;

            outputFile << curr_time << " , " << state.cameraMidExposureTimestamp << " , " << current_motor_vel << " , " << state.x << " , " << state.y << " , " << state.z << " , " << state.qx << " , " << state.qy << " , " << state.qz << " , " << state.qw  << " , " << x_extrapolated << " , " << y_extrapolated << " , " << angle_extrapolated << " , " << xc << " , " << yc << " , " << ix << " , " << iy << " , " << ir << "\n";
        }
    }

    Motor::Pause();
    Motor::Serial_close();
    outputFile.close();

    return 0;
}

// // motor test only
// int main(int argc, char *argv[])
// {
//     // init GPIO and lauch motor control
//     float v = Motor::Serial_open();
//     if(v)
//     {
//         std::cout << "Serial init failed!" << std::endl;

//         return v;
//     }
//     std::cout << "Serial init finished!" << std::endl;

//     Motor::Resume();
//     Motor::Clear_loops();
//     Motor::Set_multi_loop_position_2(0, 36000);
//     gpioDelay(2000000);

//     std::cout << "Init finished!" << std::endl;

//     while (true)
//     {
//         // delay for 1s
//         gpioDelay(1000000.0F);
        
//         int v;
//         std::cin >> v;
//         std::cout << "Velocity set to " << v << std::endl;

//         Motor::Set_velocity(v);
//     }

//     Motor::Pause();
//     Motor::Serial_close();

//     return 0;
// }

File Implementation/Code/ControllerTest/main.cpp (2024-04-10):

#include "motor.hpp"
#include <cstring>
#include <pigpio.h>
#include <iostream>

#include <fcntl.h>
#include <unistd.h>
#include <sys/ioctl.h>
#include <linux/joystick.h>

#include <errno.h>

#define _USE_MATH_DEFINES
#include <cmath>

// port of joystick
#define JOY_DEV "/dev/input/js0"

// driving speed in 0.01deg/s
#define MIN_DRV_SPD 15000.0F
#define MAX_DRV_SPD 24000.0F

// if joystick is inverted in Y
#define JOYSTICK_INVERTED 1

#if JOYSTICK_INVERTED
#define JOYSTICK_SIGN -1
#else
#define JOYSTICK_SIGN 1
#endif

// if you want the code to wait for the Bluetooth to startup and joystick to connect instead of directly quitting.
// required if you want the program to start on boot.
#define WAIT_FOR_CONNECTION 1

// record rollbot's state
// state machine is like
// disengaged <-> engaged -> running -> disengaged
enum Rollbot_state
{
    disengaged = 0,
    engaged,
    running
};

// speed control stick
enum Rollbot_ctrl
{
    RT = 4,
    LT = 5,
    LY = 1,
    RY = 3
};

int main()
{
    printf("------ Init begins! ------\n");

    // init GPIO and lauch motor control
    float v = Motor::Serial_open();
    if (v)
    {
        printf("Serial init failed!\n");
        return v;
    }
    printf("Serial init finished!\n");

    int64_t t_temp = 0, t_quit = 0, t_no_response = 0;

    Motor::Resume();
    Motor::Clear_loops();
    Motor::Set_multi_loop_position_2(0, 36000);
    Motor::Pause();
    gpioDelay(2000000);

    printf("Motor Init finished!\n");

    int joy_fd, *axis = NULL, num_of_axis = 0, num_of_buttons = 0, num_of_axis_old = -1, num_of_buttons_old = -1;
    char *button = NULL, name_of_joystick[80];
    struct js_event js;

joystick_init_start:
#if WAIT_FOR_CONNECTION
    printf("Wait for joystick connection...\n");
    while ((joy_fd = open(JOY_DEV, O_RDONLY)) == -1)
    {
        gpioDelay(100000);
    }
#else
    if ((joy_fd = open(JOY_DEV, O_RDONLY)) == -1)
    {
        printf("Couldn't open joystick!!!\n");
        return -1;
    }
#endif

    ioctl(joy_fd, JSIOCGAXES, &num_of_axis);
    ioctl(joy_fd, JSIOCGBUTTONS, &num_of_buttons);
    ioctl(joy_fd, JSIOCGNAME(80), &name_of_joystick);

    if (num_of_axis_old != num_of_axis || num_of_buttons_old != num_of_buttons)
    {
        if (axis)
        {
            free(axis);
        }
        if (button)
        {
            free(button);
        }

        axis = (int *)calloc(num_of_axis, sizeof(int));
        button = (char *)calloc(num_of_buttons, sizeof(char));

        num_of_axis_old = num_of_axis;
        num_of_buttons_old = num_of_buttons;
    }

    printf("Joystick detected: %s\n\t%d axis\n\t%d buttons\n", name_of_joystick, num_of_axis, num_of_buttons);
    fcntl(joy_fd, F_SETFL, O_NONBLOCK); /* use non-blocking mode */

    printf("------ Init successful! ------\n\n");

    t_no_response = 0;
    Rollbot_state curr_state = Rollbot_state::disengaged;
    Rollbot_ctrl curr_ctrl = Rollbot_ctrl::RT;

    while (true)
    {
        /* read the joystick state */
        if (read(joy_fd, &js, sizeof(js)) == -1)
        {
#if WAIT_FOR_CONNECTION
            // reboot if no updates in 15s
            if (t_no_response == 0)
            {
                t_no_response = Get_time();
            }
            else if (Get_time() - t_no_response >= 20000000)
            {

                close(joy_fd);
                printf("Joystick disconnected!\n");
                goto joystick_init_start;
            }
#endif
        }
        else
        {
            t_no_response = 0;
        }

        /* see what to do with the event */
        switch (js.type & ~JS_EVENT_INIT)
        {
        case JS_EVENT_AXIS:
            axis[js.number] = js.value;
            break;
        case JS_EVENT_BUTTON:
            button[js.number] = js.value;
            break;
        }

        // // for test
        // for(int i=0;i<num_of_axis;i++)
        // {
        //     printf("AXIS %d: %d  ",i,axis[i]);
        // }
        // for(int i=0;i<num_of_buttons;i++)
        // {
        //     printf("BUTTON %d: %d  ",i,button[i]);
        // }
        // printf("\n");

        switch (curr_state)
        {
        case Rollbot_state::disengaged: // motor power off, safe
            // engage when X and B are pressed but A and Y are not and hold for 1s
            if (button[1] && button[3] && (button[0] == 0) && (button[4] == 0))
            {
                if (t_temp == 0)
                {
                    t_temp = Get_time();
                }
                else if (Get_time() - t_temp >= 1000000)
                {
                    curr_state = Rollbot_state::engaged;

                    Motor::Resume();
                    Motor::Clear_loops();
                    Motor::Set_multi_loop_position_2(0, 36000);

                    printf("Motor engaged!\n");
                }
            }
            else
            {
                t_temp = 0;
            }
            break;

        case Rollbot_state::engaged: // motor armed but will not react, not safe
            // click Lmenu and Rmenu together to switch to running
            if (button[10] && button[11])
            {
                curr_state = Rollbot_state::running;

                printf("Motor running!\n");
            }
            // switch back to disengaged mode when RB and LB are pressed.
            else if (button[6] && button[7])
            {
                curr_state = disengaged;
                Motor::Pause();

                printf("Motor disengaged!\n");
            }
            break;

        case Rollbot_state::running: // motor spinning
            // switch back to disengaged mode when RB and LB are pressed.
            if (button[6] && button[7])
            {
                curr_state = Rollbot_state::disengaged;
                Motor::Pause();

                printf("Motor disengaged!\n");
                break;
            }

            Motor::Set_velocity(int32_t((MAX_DRV_SPD + MIN_DRV_SPD) / 2 + float(axis[int(curr_ctrl)] * ((int(curr_ctrl) <= 3) ? JOYSTICK_SIGN : 1)) / 32767.0F * (MAX_DRV_SPD - MIN_DRV_SPD) / 2));
            // Motor::Set_multi_loop_position_2(float(axis[int(curr_ctrl)]*((int(curr_ctrl)<=3)?JOYSTICK_SIGN:1))/32767.0F*180.0F,36000);
            // printf("Set angle to %.1f deg\n",float(axis[int(curr_ctrl)]*((int(curr_ctrl)<=3)?JOYSTICK_SIGN:1))/32767.0F*180.0F);
            break;
        }
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
